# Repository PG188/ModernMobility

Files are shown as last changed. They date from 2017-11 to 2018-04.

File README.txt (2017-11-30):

# ModernMobility
2017-2018 Tron Capstone

The objective of this project is to create a smart, semi-autonomous, medical walker. The lists below include the primary and secondary goals identified for this project. These goals are the anticipated features for the target user within this design project. 

#Primary Goals
1. Modify a standard walker to autonomously drive itself away to a ‘station’ when the user no longer requires the walker. The walker can autonomously track, navigate, and move to the a predefined ‘stations’. 
2. User can remotely prompt the walker to return to them from the product’s current location. 
3. The walker will be capable of actively braking upon detecting any rapid changes in elevation. For example, if a steep slope, stairs, or a sudden drop in the ground is detected. 
4. Maintain the primary functionalities of the common medical walker while augmenting its functionality by adding features in line with the above goals.

#Usefull GIT commands
##fetch all files from master
git fetch origin
git reset --hard origin/master

##git Resources
https://www.git-tower.com/blog/git-cheat-sheet

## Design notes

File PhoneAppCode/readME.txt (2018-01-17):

/**READ ME
* Currently app acts only as a Bluetooth client
* CAN establish a connection with a Bluetooth server
* CAN send data to server once Bluetooth connected
* CANNOT enable devices' Bluetooth
* CANNOT scan for other Bluetooth devices
* CANNOT pair with other Bluetooth devices*/

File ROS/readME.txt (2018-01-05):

Current files:
- Differential_drive is the prebuilt package that converts the velocity command from the navigation stack into individual motor torque commands to be executed by the motor controller
- node_test_1 is a package that contains the incomplete implementations for the nodes that will perform motor control and communication with the arduino connected to the ultrasound sensors. It also launches the differential_drive package, which interacts with the aforementioned nodes to create a complete control loop. 

Trying node_test_1: To try these, you must copy both the differential_drive and node_test_1 folders in your catkin workspace. You must then build them by running catkin_make in your catkin workspace directory. You must then run the launch file in the node_test_1 package using roslaunch. 

You may receive an error about 'Pyside'. To remedy this, execute the following commands which will install the correct files you need:
sudo add-apt-repository ppa:pyside
sudo apt-get update
sudo apt-get install python-pyside

This directory is for files related for ROS applications.

ROS PI SETUP:
Set up
1) Download SD Card Formatter:https://www.sdcard.org/downloads/formatter_4/
2) Download Win32DiskImager: https://sourceforge.net/projects/win32diskimager/
3) Download UBUNTU image: https://ubuntu-mate.org/download/
4) Run SD Card Formatter, select the drive that you have your SD card connected to (i.e. drive E:) and format the SD Card (it will be wiped) 
5) Extract the ubuntu-mate .img file
6) Run Win32DiskImager, select the ubuntu-mate .img file, and have it write to the drive with your SD card that you just formatted
7) Put SD card into pi, power it on, go through ubuntu-mate initial settings
8) Open terminal in ubuntu-mate and follow the ROS install instructions: http://wiki.ros.org/kinetic/Installation/Ubuntu (use full desktop install)

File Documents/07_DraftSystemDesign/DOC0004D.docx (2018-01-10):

# DRAFT SYSTEM DESIGN

# DOCUMENT

MECHATRONICS 4TB6

GROUP 2

NATHAN FUJIMOTO

PRAKHAR GARG

JOSH GILMOUR

AARON JASS

TYLER JASS

FAUZIA KHANUM

JACK LIU

GAGAN SINGH

# Table of Contents

# Table of Figures

# Table of Tables

# Revision History

Rev | Author(s) | Description of Change | Peer Reviewed | Date
- | T.Jass | Original Document | T.Jass A.Jass N.Fujimoto J.Gilmour P.Garg G.Singh F.Khanum J.Liu | 01-Dec-2017
A | T.Jass A.Jass N.Fujimoto J.Gilmour P.Garg G.Singh F.Khanum J.Liu | Added initial rough draft of content. | T.Jass A.Jass N.Fujimoto J.Gilmour P.Garg G.Singh F.Khanum J.Liu | 05-Dec-2017
B | T.Jass A.Jass N.Fujimoto J.Gilmour P.Garg G.Singh F.Khanum J.Liu | Added first draft of diagrams and added more content. | T.Jass A.Jass N.Fujimoto J.Gilmour P.Garg F.Khanum | 14-Dec-2017
C | T.Jass A.Jass N.Fujimoto J.Gilmour P.Garg F.Khanum | Updated diagrams and refined content. | T.Jass A.Jass N.Fujimoto J.Gilmour P.Garg F.Khanum | 20-Dec-2017
D | T.Jass A.Jass N.Fujimoto J.Gilmour P.Garg F.Khanum | Filling in missing content and finalized report format. | | 21-Dec-2017

# Purpose

This document’s purpose is to define and portray the overall system design of all the SmartWalker capstone project. The designs in this document considers all system requirements, defined in the SmartWalker System Requirements document. The document will communicate all the necessary designs for each functional component of the SmartWalker. By the end, the reader should have a clear understanding of what each component is, and how its design meets and satisfies the requirements. The System Design document will be used to begin implementation of the SmartWalker.

# Scope

The scope of this project is to design a walker with autonomous abilities to operate within a specific environment. The operating environment includes and is limited to the inside of a hospital (Patient rooms, staff lounges, hallways, common space). This does not include outside property belonging to a hospital. Outside of the operating environment the SmartWalker will operate as a standard wheeled medical walker.

This project will include (in scope) the following items:

- Autonomous driving (see Section 7.1 for details) between the user and docking station within one indoor room at a time. The docking station is a temporary storage location with charging capabilities.
- Obstacle avoidance in Autonomous mode.
- Assistive walking when using the SmartWalker is in Manual mode (see 7.2 Manual for details).
- Emergency braking (See section 8 for details) if approaching a steep drop in elevation (such as a staircase).
- Location tracking of the SmartWalker within the operating environment.

This project will not include (out of scope) the following items:

- Autonomous usage in multiple indoor rooms simultaneously (autonomous movement is limited to one room).
- Global Positioning system (GPS) tracking

The end result of this project will demonstrate the students’ cumulative learning through their academic career via a demonstration of the SmartWalker’s autonomous ability in a predetermined location. The SmartWalker herein referred to as walker.

# 1 Context Diagram of Boundaries

The System Context Diagram gives a high-level overview of the information passed to the major system components. The entities and interactions between them are described in Table 1 - Entity Descriptions and Interactions. More detailed information can be seen in 2 System Data Flow Diagram.

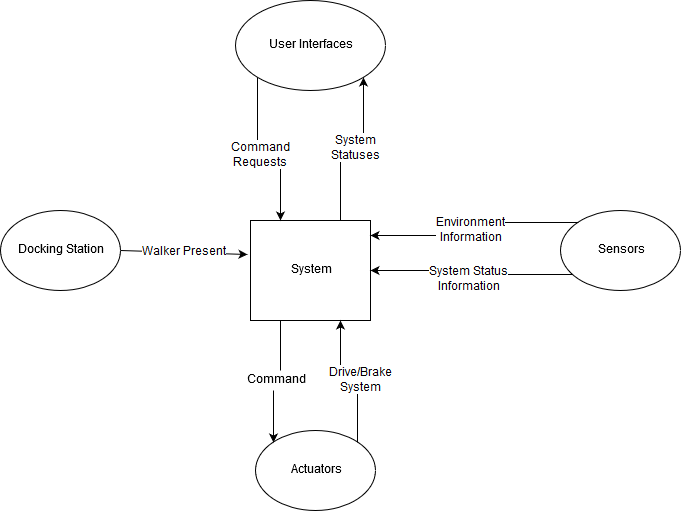
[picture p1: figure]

Figure 1 - Context Diagram of Boundaries

Table 1 - Entity Descriptions and Interactions

Entities | Entity Description | Entity Interactions | Interaction Description
System | The core of all operations. The "system" manages all of the information, computes required information, and outputs information needed by other entities. | See rows below.
User Interfaces | These are the components that the user uses to interact with the system, this would include the phone application and the on-board touch screen. | Command Requests | This will usually be a request to move to a target location or to stop.
| | System Statuses | This is any information about the system that may be useful to the user; Including the battery level, the operational mode of the walker, and the walker's current state.
Docking Station | The docking station is the walker's "Home", it is where it goes to charge. | Walker Present | Indicates to the system whether or not the walker is physically attached to the docking station.
Actuators | Components that execute a physical action. This would include the system's motors. | Command | Commanded operation to the actuator.
| | Drive/Brake System | The output action of the actuator based on the command received.
Sensors | Components that monitor and measure environment or internal information. This information would include the system's camera vision sensor, proximity sensors, and encoders. | Environment Information | Information gathered by the depth and proximity sensors used in obstacle avoidance and navigation.
| | System Status Information | Sensors that retrieve information about the system, such as encoder counts or battery level.

# 2 System Data Flow Diagram

The system Data Flow diagram shows how the different components of the system interact with each other, and with their respective inputs and outputs. The centre of all operations is the Raspberry Pi, which is effectively both the brain and the lesion controlling the flow of all information going in and out of the system.

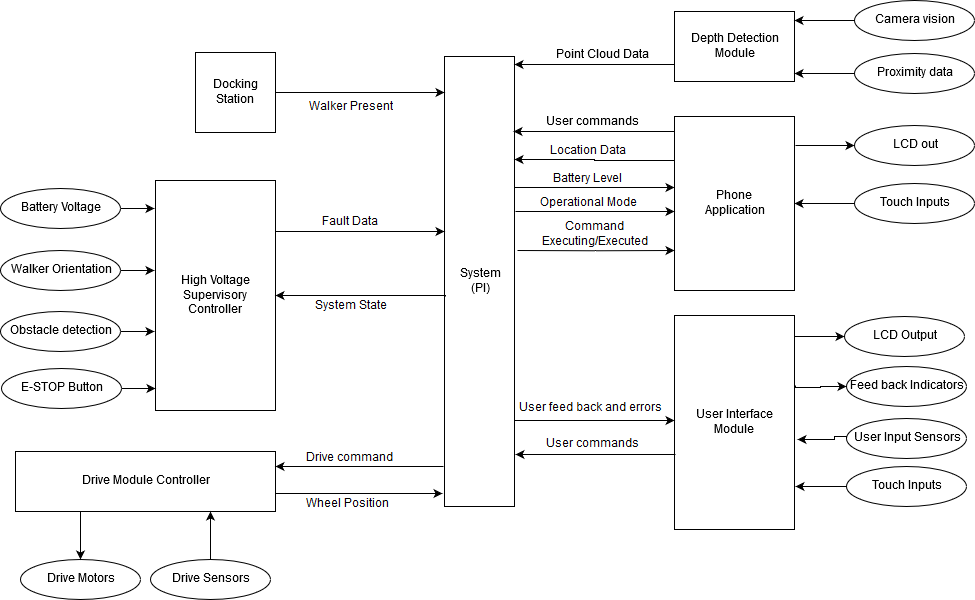
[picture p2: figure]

Figure 2 - System Data Flow Diagram

# 3 Monitored and Controlled Variables

Table 2 - Monitored Variables

Variable | Description | Units | Range
m_battery_lvl | Power level of battery. | Battery Sustain of Charge (%) | [0, 100]
m_battery_rel | Reliability of the battery. | Battery Health (%) | [0, 100]
m_proximity_in_L | Proximity to any objects in the environment (front-left side). | Distance (cm) | [0, 500]
m_proximity_in_R | Proximity to objects in the environment (front-right side). | Distance (cm) | [0, 500]
m_depth_in | Depth of the upcoming ground with respect to the bottom of the walker. | Distance (cm) | [-100, 0]
m_walker_yaw | Orientation of the walker (yaw) with respect to the walker’s z-axis. | Angle (deg) | [-180, 180]
m_walker_pitch | Orientation of the walker (pitch) with respect to the walker’s y-axis. | Angle (deg) | [-45, 45]
m_walker_loc_out | Global location of the walker. | [Longitude (deg), Latitude (deg)] | [-180, 180; -90,90]
m_walker_loc_in | Location of the walker inside the patient room, with respect to a preset coordinate system. | [x,y] on room map | [0, 100; 0, 100]
m_human_loc_in | Location of the human based on their phone, with respect to a preset coordinate system. | [x, y] on room map | [0, 100; 0, 100]
m_human_yaw | Orientation of the human (yaw) with respect to the human’s z-axis. | Angle (deg) | [-45, 45]
m_desired_loc | User selected desired location for the walker in autonomous mode | Enum (states) | GoDocking, GoHuman
m_dock_aligned | Walker is physically aligned with the docking station | Boolean | 0, 1
m_user_in_L | Desired forward assisted movement for the user, for the left motor. | Custom | [-100,100]
m_user_in_R | Desired forward assisted movement for the user, for the left motor. | Custom | [-100,100]
m_emergency_signal | Signal for monitoring an emergency situation. | Boolean | 0, 1

Table 3 - Controlled Variables

Variable | Description | Units | Range
c_motorL_speed | Left motor speed. | Angular velocity ( deg/s) | [0, 50]
c_motorR_speed | Right motor speed. | Angular velocity (deg/s) | [0, 50]
c_brakeL_position | Left brake position. | Brake Position (%) | [0, 100]
c_brakeR_position | Right brake position. | Brake Position (%) | [0, 100]
c_charge_walker | Charge the walker. | Boolean | 0, 1
c_dock_connected | Walker physically connected to the docking station. | Boolean | 0, 1

# 4 Constants

1. Number of kinect sensors
2. Location and orientation of kinect sensors
3. Number of ultrasound sensors
4. Location and orientation of ultrasound sensors
5. Location and orientation of docking station
6. Reference orientation of the user and robot
7. Origin of estimote coordinate frame
8. Location of estimotes in the room
9. Overall walker shape (parameter of differential package in ROS)
10. PID Coefficients for motor controllers
11. Voltage the walker runs on
12. Number of Arduinos
13. Number of Raspberry Pis
14. Number of motor-actuated wheels, motor control boards, and encoders
15. Maximum speed of the walker during autonomous navigation
16. Minimum allowable distance to obstacles while autonomously navigating
17. Distance in front of user that walker should initially navigate too
18. How close the walker should come to the user after initial navigation

# 5 Behaviour Overview

## 5.1 Overall System Behaviour

The behaviour of the walker system can be seen by the following behavioural state diagrams. To describe at the main behavioural components of the walker system, three state diagrams were outlined: the overall system behaviour diagram, the autonomous behaviour diagram, and the manual mode behaviour diagram. The latter two main sub states in which the walker primarily operates in. In any state, the walker is perceiving information from the environment for both functioning and state transitioning.

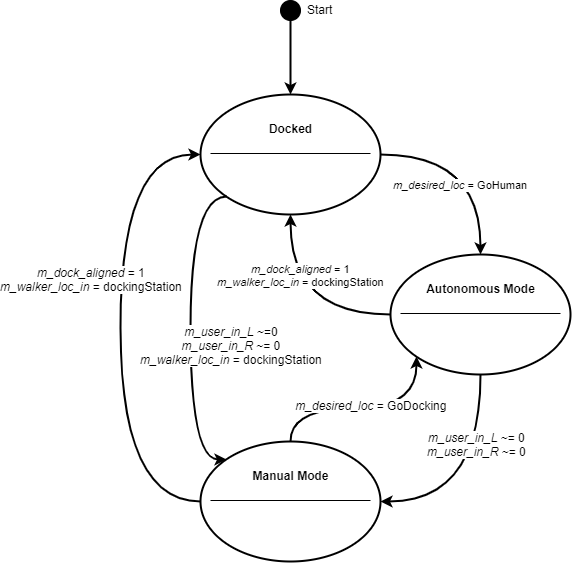
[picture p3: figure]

Figure 3 - Overall System Behaviour Diagram

Table 4 - State Behaviour

State | Description
Docked | In this state the walker is physically connected to the docking station. When connected, the walker is charging its onboard power supply.
Autonomous Mode | In this state the walker is autonomously navigating to and from the user and the docking station (or its current position).
Manual Mode | In this state the walker is being manually operated by the user. This is intended as standard walker usage, with additional safety features.

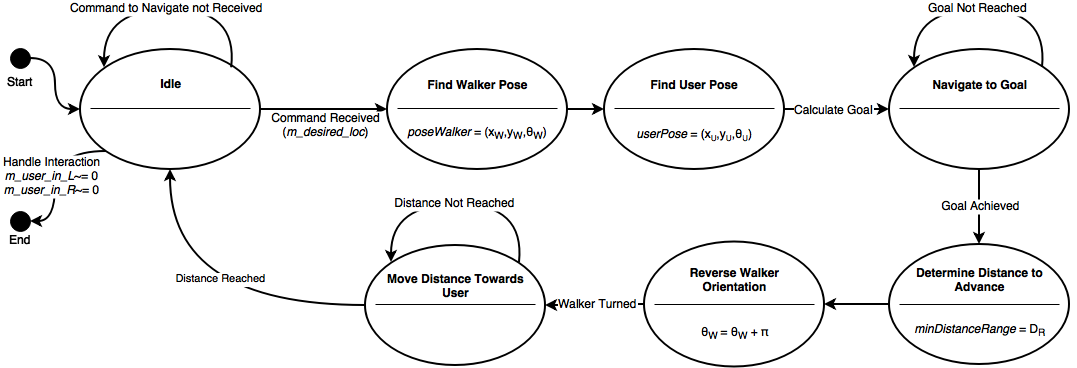
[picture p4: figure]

Figure 4 - Autonomous Mode Behaviour Diagram

Please note, whenever the walker is put into an unintended event, a safety check will be done of the status of the system, and the status will be fixed if possible and sent back to the idle position.

Table 5 - Autonomous Mode States

State | Description
Idle | In this state the walker is in a waiting phase where it is waiting on instructions on where to navigate by the user, via the user interface.
Find Walker Pose | In this state the walker determines its relative position on the constructed map grid, as well as its relative yaw angle on the map.
Find User Pose | In this state the walker system determines the relative position of the user on the constructed map grid, as well as the user’s relative yaw angle on the map.
Navigate to Goal | In this state, considering the walker pose and user pose, the walker calculates the navigation goal and thus begins to navigate to the location.
Determine Distance to Advance | In this state the walker determines how far it can safely approach the destination.
Reverse Walker Orientation | In this state the walker orientates its yaw relative yaw angle so that its handles are facing the user (180-degree turn).
Move Distance Towards User | In this state the walker creeps until it has reached the safe approaching distance. The system then goes back to the idle state.

As described in the overall system behaviour diagram, if either the walker has reached the docking station or the user physically interacts with walker will the behaviour exit the autonomous mode.

## 5.2 Navigation Goal Calculation

The walker and user pose will both be determined by the beacons in the room. The goal is the location where the robot is supposed to travel based on where the user is. The goal is calculated to be some distance, K, in front of the user. It is calculated as:

Figure 5 - Navigation Goal Calculation

The pi added to the user orientation ensures that the walker is facing the user at the end of navigation. This facilitates the measurement of distance between the walker and user in the next state. The walker is then to turn around and approach the user to a reasonable distance (to be determined).

Figure 6 - Manual Mode Behaviour Diagram

Table 6 - Manual Mode States

State | Description
Idle | In this state the walker is in a waiting phase where it awaits physical interaction from the user, in the form of the handle sliders being moved.
Check if Walker is Safe | In this state the walker immediately checks the environment if there are any detectable dangerous obstacles or landmarks in the vicinity of the walker.
Walker in Use | Once the system deems it is safe, in this state the walker operates like a traditional walker, where it helps the user move him or herself.
Emergency Detected | In this state an emergency was detected and the walker brakes so it cannot be further moved. A safety check is completed so the emergency situation is no longer present.

Please note, the Emergency Detected includes the detection of any hazardous situations the user is in the vicinity of (oncoming drops, large slopes, etc..). The safety check will enact functionality to aid the user if wished to proceed through the hazard, if possible (please refer to Section 7 - Normal Operation) Manual mode behaviour is left when the user asks for the walker to navigate back to the docking station, or to a new position where the user would be.

# 6 Component Details

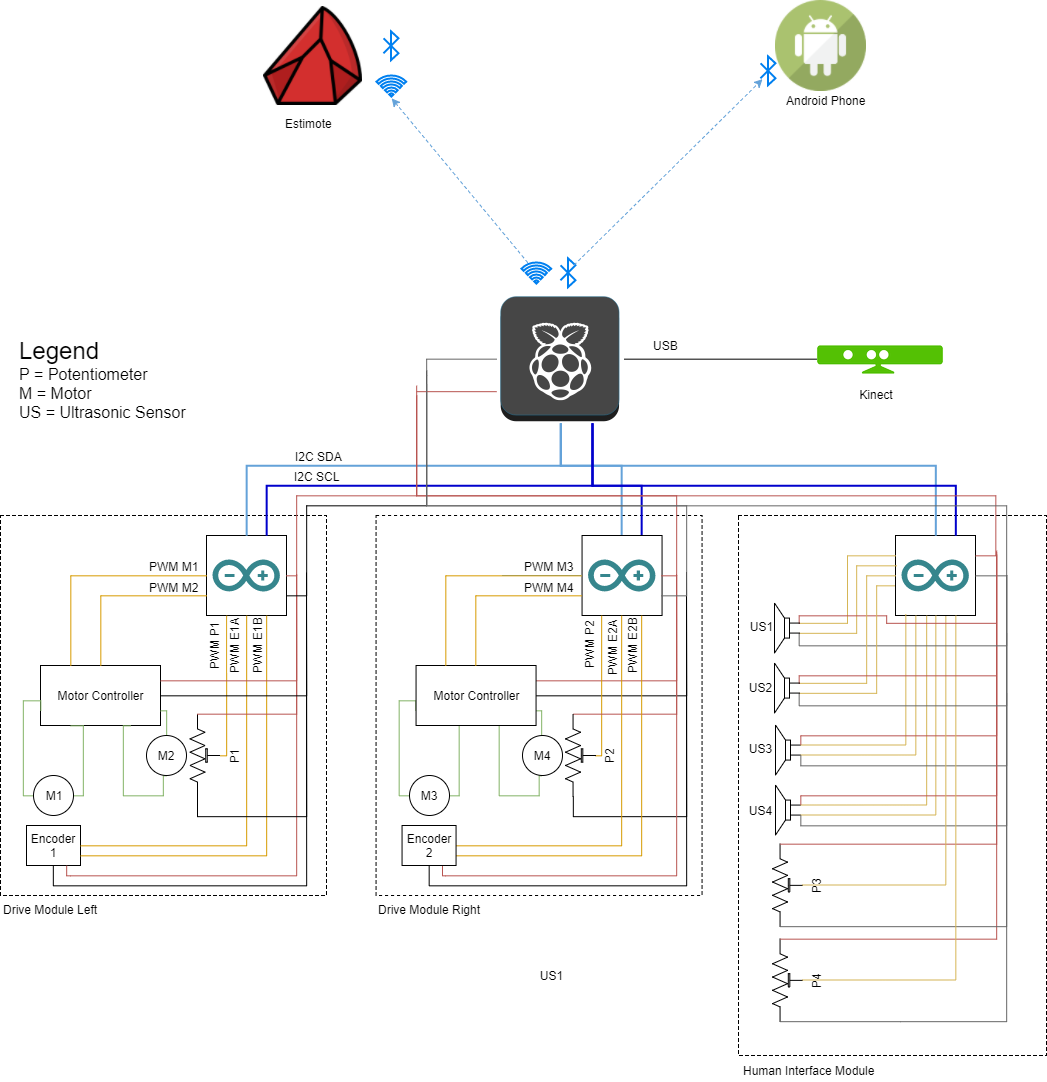
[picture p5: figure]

Table 7 - Component Descriptions

Component | Inputs | Outputs | Description
Raspberry Pi | Modules: - Microsoft Kinect - Estimotes - Android Mobile Phone | Modules: - Drive Module Left - Drive Module Right - Human Interface Module | The main supervisory module in the walker System. It directs data to and from the other modules to assure functionality.
Estimotes | Monitored Variables: - m_walker_loc_in | Modules: - Raspberry Pi | Wireless beacons to be used for indoor location and navigation of the walker System.
Android Phone | Monitored Variables: - m_human_loc_in - m_human_yaw - m_desired_loc | Modules: - Raspberry Pi | The assumed personal electronic device that is owned by the user. This device will host the walker Application that will transmit commands and user location information, and receive system system status information.
Kinect (Sensory Module) | Monitored Variables: - m_proximity_in_L - m_proximity_in_R - m_depth_in - m_walker_yaw - m_walker_pitch | Modules: - Raspberry Pi | Sensor returning point cloud data about the environment. This sensor is vital to the system’s object detection.
Drive Modules | Modules: - Raspberry Pi - Human Interface Module | Control Variables: - c_motorL_speed - c_motorR_speed - c_brakeL_position - c_brakeR_position | Modules that will do computations on the internal system data and external environment data from the sensors and use it to control the actuators (motors) appropriately.
Human Interface Module | Monitored Variables: - m_user_in_L - m_user_in_R - m_emergency_signal Modules: - Raspberry Pi | Modules: - Drive Modules | This module is the physical interface between the drive module and the user. It allows the user to manually drive the walker system’s motors.

Table 8 - Derived Timing Constraints

Module | Derive Timing Constraints
Kinect | Cannot read data from the Kinect faster than the Raspberry Pi can process it whilst also maintaining other system functionality
Android Phone | Will communicate messages from the user at the standard Bluetooth 4.0 speeds to the Raspberry Pi (on the walker), and back to the user.
Estimotes | The beacon responsiveness will adhere to the Raspberry Pi’s scanning of the beacons while in Autonomous Mode.
Raspberry Pi | Must communicate with the arduinos at a rate they can handle and are configured to accept.
Drive Modules | Arduinos must communicate with the Pi and motor controllers at a rate they can handle and are configured to accept. The arduinos must run fast enough that it does not miss any encoder counts and are able to keep up with the rate of them.
Human Interface Module | The status of the human and environment interactions must be checked often enough that no user interactions are missed. Braking inputs and ultrasonic data will adhere to serial ‘I-squared-C’ speeds for sending data to the Raspberry Pi and to the Drive Modules.

Table 9 - Initialization

Module | Initialization
Kinect | Run the libfreenect driver to allow reading data from the Kinect.
Android Phone | The app must be running on the phone and a bluetooth connection established with the walker before several walker features can be used, such as autonomous navigation.
Estimotes | Physically the beacons required to be on the walls of the room, at the centre of each wall. Additionally, one would have to be inside the walker and connected to the Raspberry Pi at initialization.
Raspberry Pi | The Raspberry Pi will be turned on and have the necessary software pre-installed.
Drive Modules | The Arduinos, motor controllers, motors, and encoders will all have to be turned on via power-up. The arduinos will have the necessary software pre-installed.
Human Interface Module | The arduino and the sensors to interact with the human and environment (brakes and ultrasonic) will be initialized at power-up.

# 7 Normal Operation

The following section will describe the different modes and states each mode has in more detail by stepping through possible positive normal scenarios.

Please note since this is the Draft System Design that we have not determined all details yet and have noted said details to be defined later.

## 7.1 Autonomous

As mentioned in our System Requirements document, autonomous mode is the ability to move out to a designated home location as well as return to the user when requested. Autonomous mode consists 3 states: moving to user, moving to docking station, and docked. The following sections will describe positive normal scenarios (behaviour the system should cover and everything proceeds as expected).

### 7.1.1 Moving to user

1. User is not detected by handlebar sensors (m_user_in_L and m_user_in_R)
2. User requests the walker to come to user via phone app
3. Phone app sends bluetooth signal to walker
4. If walker is not within bluetooth distance?
  a. Display message to user “Walker out of reach.”
5. If walker is within bluetooth distance
  a. Walker retrieves walker pose from estimotes
  b. Walker retrieves user pose from estimotes
  c. Walker calculates the goal pose and begins navigating to it, as described before
  d. Once the walker reaches the goal, the distance to the user is measured
  e. The walker turns 180 degrees
  f. The walker backs up to within a reasonable distance from the user
  g. Walker returns to idle state

### 7.1.2 Moving to docking station

1. User is not detected by handlebar sensors (m_user_in_L and m_user_in_R)
2. User sends signal to dock via phone app
3. If walker is not within bluetooth distance
  a. Display message to user “Walker out of reach.”
4. If walker is within bluetooth distance
  h. Walker retrieves walker pose from estimotes
  i. Walker retrieves docking station pose from estimotes
  j. Walker moves to docking station
  k. Walker docks into charging port (m_dock_aligned)
    i. Go to Docked state

### 7.1.3 Docked

1. Walker is at the docking station and connected (c_dock_connected)
  a. If battery is less than 100% (m_battery_lvl)
      1. charge (c_charge_walker)
    i. If battery is at 100% (m_battery_lvl)
      1. Disengage charging and go to Idle state

## 7.2 Manual

As mentioned in our System Requirements document, Manual mode is the ability to operate like a standard medical walker, with added smart features such as assisted braking and assisted driving. Manual mode has 4 states: regular walking, slope change, objects detected, and idle. The following sections will describe positive normal scenarios (behaviour the system should cover and everything proceeds as expected).

### 7.2.1 Regular Walking

This state is when the user is utilizing the walker as intended; aiding in regular walking.

1. User detected at handlebar sensors (m_user_in_L and m_user_in_R)
  a. Detect if the walker is moving and surrounding environment
    i. Slope change → Slope Change mode
    ii. Objects in way → Objects detected
    iii. User is utilizing walker for normal walking
  b. User applies brakes manually (c_brakeL_position and c_brakeR_position)
    i. reduce speed accordingly
2. If user is not detected (for more than a certain amount of time, to be determined)
  a. Enter idle state

### 7.2.2 Slope Change

This state is for when the user is detected at the handlebar sensors, the user is walking around with the aid of the walker and the smartwalker has detected a change in slope of the ground.

1. Query the slope of the ground using the onboard sensors
2. Calculate the pitch of the walker (m_walker_pitch)
3. If the pitch of the walker is positive or negative 5 deg to a certain deg
  a. This state has yet to be finalized, more details to come in the future

### 7.2.3 Idle

1. User is not detected at handlebar sensors (m_user_in_L and m_user_in_R)
  a. If walker is not detected at docking station (m_dock_aligned)
- Walker waits for command from user
  b. If walker is detected at docking station (m_dock_aligned)
    - If battery is less than 100% (m_battery_lvl)
      - charge walker (c_charge_walker)
    - If battery is 100% (m_battery_lvl)
      - Sit idle (details of idle mode to be determined)

# 8 Undesired Event Handling

Section 7 covered normal operation of the walker, this section will talk about abnormal scenarios and how the walker will handle them. Each section will describe the undesired event and the steps the system will take to ensure that the event is resolved in a safe manner.

## 8.1 Emergency Stop

Emergency stop refers to when the user pushes/applies the emergency stop or the system determines that there is an emergency and sends a signal at any point while the walker is in normal operation. This option is for when the user

1. Emergency Stop activated
  a. Brakes applied to motors in a safe manner (c_brakeL_position and c_brakeR_position)
  b. State of emergency (walkerSafe = False)
  c. Display prompt for user to cancel emergency state
  d. Wait for user input
    i. Safe to continue OR enter manual mode (cancel initial request)

## 8.2 User Detected During Autonomous Mode

The following scenario is for the walker is in autonomous mode and a user is detected by the handlebar sensors.

1. Walker is in autonomous mode
2. User is detected by handlebar sensors (m_user_in_L and m_user_in_R)
a. Brakes applied to motors in a safe manner (c_brakeL_position and c_brakeR_position)
b. Walker enters manual mode

## 8.3 Object Collision with Smartwalker

The following scenario is for when the smartwalker is in autonomous mode and has collided with an object of a minimum size yet to be determined.

1. Walker location does not match expected location
a. Brakes applied to motors in a safe manner (c_brakeL_position and c_brakeR_position)
b. State of emergency (walkerSafe = False)
c. Wait for user input
  i. Safe to continue OR enter manual mode (cancel initial request)

## 8.4 Walker has Fallen Over or Very high Incline/Decline

This state is when the walker has fallen over or is at a dangerously high incline or decline. This is a very undesired and not recommended.

1. Walker gyroscopes detect angle greater than 15°
a. Brakes applied to motors in a safe manner (c_brakeL_position and c_brakeR_position)
b. State of emergency (walkerSafe = False)
c. Wait for user input
  i. Safe to continue OR enter manual mode (cancel initial request)

## 8.5 Goal location is unreachable

When the walker is in autonomous mode, it has a goal of either the user or the docking station. In moments when the path is not clear to the destination, the following will occur:

1. Walker attempts to reach destination
2. Several attempts at reaching goal occur (attempt number and duration to be determined)
3. Walker stops attempting to reach goal
4. Go into idle mode
5. Message is sent to the user’s phone “unable to reach destination.”

## 8.6 Walker cannot “see”

The following state refers to when the walker sensors are not functioning properly either due to sensor malfunction or a blockage (items covering the sensors) and therefore reporting false data. The walker is in an environment it is not capable of reliably navigation through and thus navigation will cease autonomous mode and the walker will return to manual mode. The user is then able to move the walker to a safe location for troubleshooting.

## 8.7 Walker is unable to move while autonomously navigating

When the walker is in Autonomous mode and Autonomous navigation with cease and the walker will return to idle mode. The user will be notified via the phone application of the problem.

## 8.8 Extremely low battery

Since the walker is very dependent on power, when the battery level is very low (low level to be determined) the walker will the take the following actions.

1. User will be notified of the low battery state via the phone application
2. The walker will shut down to avoid unexpected behaviour at low power and to avoid damaging the battery

# References

Rodriguez, J. (2016, November 22). How An ADA Compliant Ramp Must be Built. Retrieved December 21, 2017, from https://www.thebalance.com/ada-ramp-construction-844440

MODERN MOBILITY DRAFT SYSTEM DESIGN DOCUMENT Doc: DOC0004 Rev: D

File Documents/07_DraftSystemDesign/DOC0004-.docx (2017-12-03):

# DRAFT SYSTEM DESIGN

# DOCUMENT

MECHATRONICS 4TB6

GROUP 2

NATHAN FUJIMOTO

PRAKHAR GARG

JOSH GILMOUR

AARON JASS

TYLER JASS

FAUZIA KHANUM

JACK LIU

GAGAN SINGH

Table of Contents

# Table of Tables

# Revision History

Rev | Author(s) | Description of Change | Peer Reviewed | Date
- | T.Jass A.Jass N.Fujimoto J.Gilmour P.Garg G.Singh F.Khanum | Original Document

# Purpose

# Scope

# 1 Context Diagram of Boundaries

2 System Component Diagrams

3 Monitored and Controlled Variables

4 Constants

5 Behaviour Overview

6 Component Details

7 Normal Operation

8 Undesired Event Handling

References

## 2.1 Tools and Versions

Table 2 - Tools and Versions

Tool | Version | Purpose/Function

Software Tools:
Google Drive | N/A | Storage accessible by entire group for deliverable documents.
Google Docs | N/A | Real-time collaboration.
Draw.io | N/A | Online web tool for model mapping and flow chart development.
Git | 2.15 | Software Version control, deliverable document, and internal document storage.
Ubuntu MATE | 3.0 | OS being used on our systems controller (Raspberry Pi 3B).
ROS (Robotics Operating System) | Kinetic | Robotics operating system library being used to develop project’s autonomous navigation capabilities.
Android Studio | 3.0 | Environment for Android App Development.
Autodesk Inventor | 2017 | Model all physical Robotics systems.

Mechanical Tools:
3D Printer | N/A | Prototype any mechanical parts for motor and braking systems.
Hand Drill | N/A | Used for drilling holes
Saw | N/A | Used for cutting material
CNC Mill | N/A | Produce finished mechanical parts for motor and braking systems.

Electrical Tools:
Soldering Iron | N/A | Soldering wires/ circuit boards
Multimeter | N/A | Measure voltage and current
Power Supply | N/A | Powering prototype circuits/Motors
Oscilloscope | N/A | Measuring electrical signals

## 2.2 Special Instructions

All document resources will be backed up to the corresponding version control systems.

## 2.3 Standards Followed

- All code should be commented to allow for quick and painless troubleshooting, our motto is “Comment as if the next person who reads your code is a serial killer”
- When coding, no function should have more lines than what can be seen on your computer screen at one time
- No software or hardware tested by the person who implemented it can deemed “Working” (basically do not test your own work, get someone else to test it)
- Metric Units will be used for all modeled components

## 2.4 Delegation of Steps

Legend

1 - Primary Responsibility

2 - Secondary Responsibility

3 - Tertiary Responsibility

Highlight - Persons Responsible for section of project

Table 3 - Delegation of Steps

| Josh | Aaron | Jack | Nathan | Fauzia | Prakhar | Tyler | Gagan
Phone application development | | 1/2 | 1 | | 3 | 2 | 3
Autonomous navigation software | 1 | | 2 | 2
Low-level software | 2 | 3 | | 1 | 1 | | 1
System integration | 3 | | 3 | | 2 | 1* | | 3
Wheels and brakes modifications | | 1/2 | | 3 | | 3 | 2 | 1
Handle Bar (brake interference) | | | | | | 1 | | 2

# 3 How Version Control is Being Used

Version control will be used to manage all source code, and as well as store documents. The source code will be organized into different directories based on the application. Documents including will be both deliverables and internal documents used for team knowledge sharing.

Our Git is organized into folders that relate to different aspects of the project. These folders are described in the table below.

Table 4 - Git Organization

Folder | Purpose
CADs | Store the CAD files created of the walker and other components
Low level | Store documentation and files related to the software built for the Arduino and Raspberry Pi
Phone application code | Store documentation and files related to the phone application that is used to control and setup the walker.
ROS | Store documentation and files related to the ROS software on the walker

# 4 Dealing with Changes to Artifacts

## 4.1 Bug Tracking/Change Request Tool

If we find that we are running into a lot of bugs and are spending quite a bit of time resolving them we will look into using Bugzilla. It is free for any number of users, compatible with Linux, MacOS, and Windows, and contain the following:

- Time tracking
- Reporting
- Duplicate bug detection
- Customization: custom fields to suit application

## 4.2 Documentation of Change Requests/Bugs

All of documentation is first drafted in Google Docs. Google Docs allows real time collaboration, commenting, and revision control. We can use this to document and track changes during the creation and drafting process. Once complete, we can export to word and finalize the document.

## 4.3 Classification of Changes

Changes will have different statuses such as:

- In queue (Waiting to be dealt with)
- Working (Currently being investigated)
- Resolved (Issue/Bug successfully dealt with)
- Unresolved (Unable to solve this issue/bug)

They should also have different levels of urgency based on how core the issue/bug is to the particular systems functionality.

## 4.4 Disposition of Changes

Change statuses will be verified and changed to different status by the appropriate party. For example, anyone can raise an issue and add them to “In Queue”. Depending on the given issue, a particular team may be responsible to fix that issue. Only that team can change that issue’s status to “Working”. Since it would bad practice to have the same person who fixed the issue, also verify the issue, someone else would be responsible for moving the issue to “Resolved”. If the person fixing the issue cannot fix it, they can move it to “Unresolved” so someone else can try it.

MODERN MOBILITY DRAFT SYSTEM DESIGN DOCUMENT Doc: DOC0004 Rev: -

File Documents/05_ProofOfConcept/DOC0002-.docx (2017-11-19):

# PROOF OF CONCEPT

# TEST REPORT DOCUMENT

MECHATRONICS 4TB6

GROUP 2

NATHAN FUJIMOTO

PRAKHAR GARG

JOSH GILMOUR

AARON JASS

TYLER JASS

FAUZIA KHANUM

JACK LIU

GAGAN SINGH

# Revision History

Rev | Author(s) | Description of Change | Peer Reviewed | Date
- | T.Jass | Original Document | N. Fujimoto A. Jass | 19/11/2017

# Document References

N/A

# Table of Tables

N/A

# Table of Figures

N/A

# 1 Required Knowledge

## 1.1 Image of Kinect

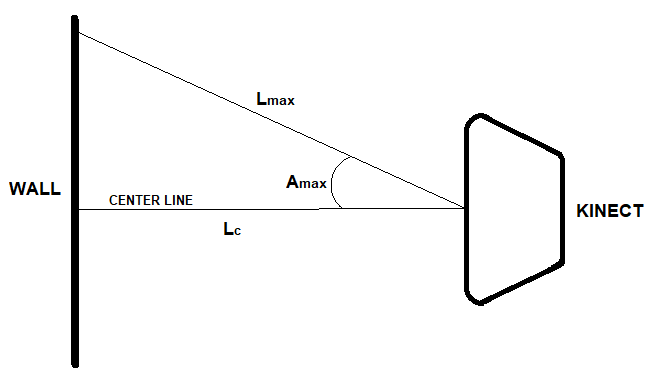
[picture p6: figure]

## 1.2 Terminology

Term | Definition
Kinect | Microsoft’s Kinect Camera
Wall | Flat wall surface used in testing
Center Line | Line of sight going straight (angle of 0 degrees) to the wall
Amax | Maximum angle from the centre line the Kinect can detect
Lmax | Length from the Kinect’s Camera to the wall at an angle of Amax
Lc | Length from the Kinect’s Camera to the wall along the center line

# 2 Procedure

1. Faced Kinect toward the wall, ensuring that the line of sight going straight was perpendicular to the wall.
2. Physically measured using a measuring tape and positioned the Kinect so that Lc = 50cm.
3. Recorded the Lc value measured by the Kinect.
4. Physically measured using a measuring tape the Lmax value.
5. Recorded the Lmax value measured by the Kinect.
6. Repeated steps 2 to 5 for Lc = 75cm, 100cm, and 125cm.
7. Repeated steps 2 to 3 for Lc = 192cm and 213cm.

# 3 Results

<Insert Graphs and excel table data>

MODERN MOBILITY PROOF OF CONCEPT TEST REPORT DOCUMENT Doc: DOC0002 Rev: -

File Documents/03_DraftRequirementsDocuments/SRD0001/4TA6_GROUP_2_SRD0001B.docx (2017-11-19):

# SMART WALKER

# SYSTEM REQUIREMENTS DOCUMENT

MECHATRONICS 4TB6

GROUP 2

NATHAN FUJIMOTO

PRAKHAR GARG

JOSH GILMOUR

AARON JASS

TYLER JASS

FAUZIA KHANUM

JACK LIU

GAGAN SINGH

Table of Contents

# Revision History

Rev | Author(s) | Description of Change | Peer Reviewed | Date
- | T.Jass | Original Document | A.Jass | 10-Oct-2017
A | N.Fujimoto P.Garg J.Gilmour A.Jass T.Jass F.Khanum J.Liu G.Singh | Original document was blank with just a layout. This revision adds content to the document. | N.Fujimoto P.Garg J.Gilmour A.Jass T.Jass F.Khanum J.Liu G.Singh | 01-Nov-2017
B | N.Fujimoto P.Garg J.Gilmour A.Jass T.Jass F.Khanum J.Liu G.Singh | Edited Functional Requirements, functional decomposition diagrams and variables, non-functional requirements. Added Systems Definitions and Requirements Subject to Change Sections. | N.Fujimoto P.Garg J.Gilmour A.Jass T.Jass F.Khanum J.Liu G.Singh | 06-Nov-2017

# Table of Tables

# Table of Figures

# 1.1 Introduction

## 1.1 Purpose

The standard medical walker or walking aid helps to improve the stability and balance of its user while they are walking. The objective of this project is to modify a standard medical walker to include various mechanical/electrical components and autonomous features in order to improve the user experience. The modified walker, called the SmartWalker, will involve designing and developing an autonomous and safe system while keeping all original functions of the standard medical walker.

This document defines the project scope, outlines the system overview and highlights the main functional and nonfunctional requirements of the SmartWalker.

## 1.2 Project Scope

The scope of this project is to design a walker with autonomous abilities to operate within a specific environment (refer to section 2.4 Operating Environment). The SmartWalker will feature:

- Autonomous driving between a docking location and the user within an indoor room, and vice-versa. The dock is a temporary storage location with charging capabilities.
- Autonomous obstacle avoidance when driving to and from the user.
- Assistive walking when using the SmartWalker normally, this includes assistive powering when going up ramps, and active braking when going down ramps.
- Emergency braking in any situation if approaching a steep drop in elevation (staircase).
- Global Position System (GPS) tracking within the environment.

This project will not include (out of scope) the following items:

- Autonomous usage in multiple indoor environments simultaneously (autonomous movement between multiple rooms).
  - Autonomous features in an entire hospital.
- Exact GPS tracking while walker is indoors.

The end result of this project will demonstrate the students’ cumulative learning through their academic career via a demonstration of the SmartWalker’s autonomous ability in a predetermined location.

# 2 Overall Description

## 2.1 System Overview

The SmartWalker is an original idea by the Modern Mobility group, within the capstone course of the Computing and Software Department, 4TB6, at McMaster University. The focus of the SmartWalker project is to increase the utility of a standard medical walker by implementing various autonomous and electric features. Full system details and functionalities are explained below.

## 2.2 System Term Definitions

Table 1 - System Term Definitions

Term | Definition
X-axis | Forward direction relative to the SmartWalker.
Y-axis | Left direction relative to the SmartWalker.
Z-axis | Upward direction (normal to the SmartWalker’s XY-plane).
Yaw | Angle from the X-axis going counter-clockwise about the Z-axis in the XY-plane.
Pitch | Angle from the Y-axis going counter-clockwise about the X-axis in the YZ-plane.
Roll | Angle from the Z-axis going counter-clockwise about the Y-axis in the XZ-plane.
Docking Station | The device that charges the SmartWalker. This is considered the SmartWalker’s Home.
UI | User Interface.
Phone App (Phone Application) | Refers to an application on a person’s smartphone device. Often simply called an “App”.

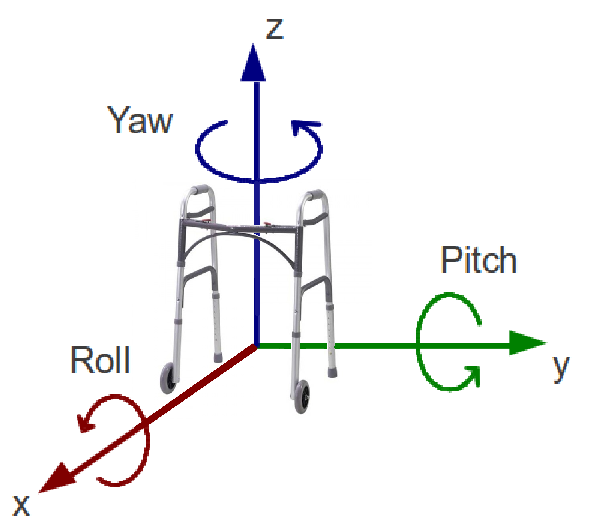
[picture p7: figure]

Figure 1 - SmartWalker Axes and Orientation

## 2.3 System Behaviour

The SmartWalker has two main functionalities (or modes): autonomous mobility and manual driving.

- Autonomous Mode: The ability to move out of the way of the user whenever requested to a designated home location as well as return to the user when requested.
- Manual Mode: The ability to operate like a standard medical walker, with added smart features like assisted braking and assisted driving.

These core functions are supported by two sub-functions: a phone application and a docking station. The phone app is used as an avenue to capture user-specific monitored variables, while the docking station is used to support the autonomous mobility function by acting as a home location.

## 2.4 Operating Environment

The operating environment of the SmartWalker is a typical hospital. This environment is divided into two areas: the patient’s room, and the hospital hallways/common rooms and outside grounds. Manual mode will be available in all environments (patient room, hospital corridors, hospital grounds etc.) while Autonomous mode will only be available in the patient room that contains its corresponding docking station.

Figure 2 below indicates a sample patient room in a hospital. The docking station would be located next to a wall plugged into an electrical outlet ready to charge the walker at any moment. The docking station will not be in the way of medical equipment and medical personnel such as doctors, nurses, and caregivers. Figure 3 below indicates a sample hospital and its surrounding outside grounds that the SmartWalker can be implemented in.

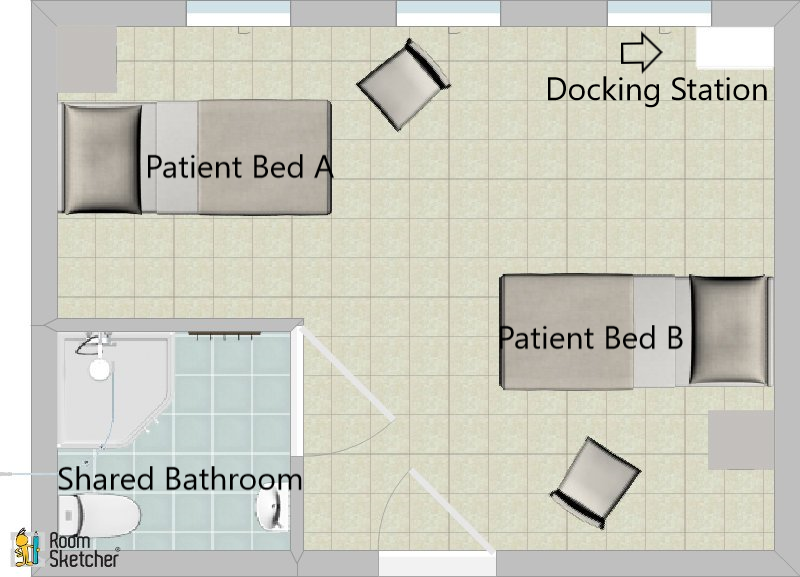
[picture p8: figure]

Figure 2 - Hospital Patient Room

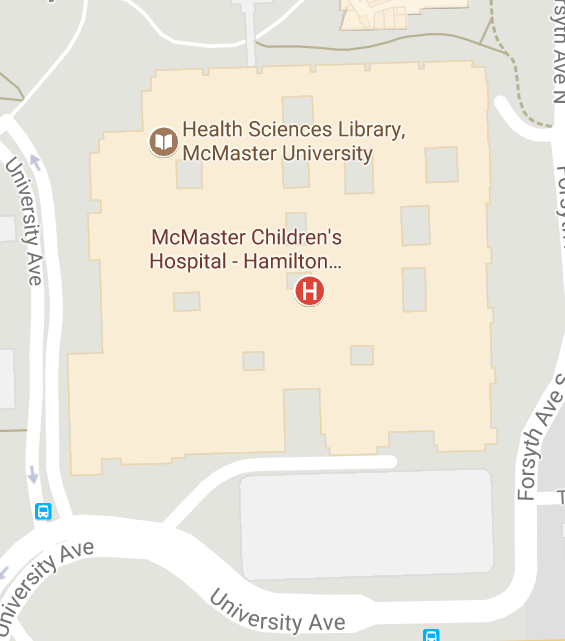
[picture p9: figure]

Figure 3 - Google Maps Image of a Hospital and Surrounding Area

## 2.5 Assumptions

### 2.5.1 Environmental Assumptions

- The SmartWalker will be used in patient rooms that have enough room for wheelchairs to move about, therefore enough room for the SmartWalker to autonomously move about
- It is assumed that the farthest the SmartWalker will be taken will the hospital grounds.

### 2.5.2 Functional Assumptions

- An structurally sound off the shelf walker will be used as the basis for the SmartWalker
- The SmartWalker battery will be charged via the docking station and no other method.

### 2.5.3 User Assumptions

- The user of the SmartWalker will have little experience interacting with technology such as phone applications.
- The user owns a phone that runs on Android OS.

## 2.6 Functional Decomposition and Variables

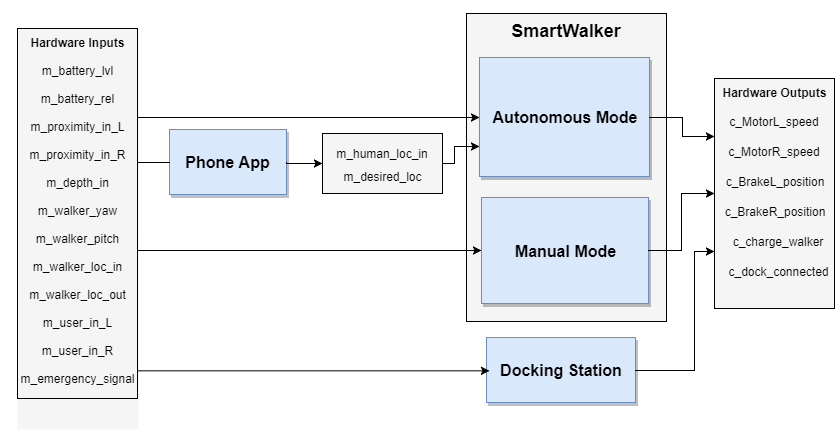
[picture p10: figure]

Figure 4 - Functional Decomposition Diagram

Table 2 - Monitored Variables

Variable | Description | Units | Range
m_battery_lvl | Power level of battery. | Battery Sustain of Charge (%) | [0, 100]
m_battery_rel | Reliability of the battery. | Battery Health (%) | [0, 100]
m_proximity_in_L | Proximity to any objects in the environment (front-left side). | Distance (cm) | [0, 500]
m_proximity_in_R | Proximity to objects in the environment (front-right side). | Distance (cm) | [0, 500]
m_depth_in | Depth of the upcoming ground with respect to the bottom of the walker. | Distance (cm) | [-100, 0]
m_walker_yaw | Orientation of the walker (yaw) with respect to the walker’s z-axis. | Angle (deg) | [-180, 180]
m_walker_pitch | Orientation of the walker (pitch) with respect to the walker’s y-axis. | Angle (deg) | [-45, 45]
m_walker_loc_out | Global location of the walker. | [Longitude (deg), Latitude (deg)] | [-180, 180; -90,90]
m_walker_loc_in | Location of the walker inside the patient room, with respect to a preset coordinate system. | [x,y] on room map | [0, 100; 0, 100]
m_human_loc_in | Location of the human based on their phone, with respect to a preset coordinate system. | [x, y] on room map | [0, 100; 0, 100]
m_desired_loc | User selected desired location for the walker in autonomous mode | Enum (states) | GoDocking, GoHuman
m_user_int_L | Desired forward assisted movement for the user, for the left motor. | Custom | [-100,100]
m_user_in_R | Desired forward assisted movement for the user, for the left motor. | Custom | [-100,100]
m_emergency_signal | Signal for monitoring an emergency situation. | Boolean | 0, 1

Table 3 - Controlled Variables

Variable | Description | Units | Range
c_motorL_speed | Left motor speed. | Angular velocity ( deg/s) | [0, 50]
c_motorR_speed | Right motor speed. | Angular velocity (deg/s) | [0, 50]
c_brakeL_position | Left brake position. | Brake Position (%) | [0, 100]
c_brakeR_position | Right brake position. | Brake Position (%) | [0, 100]
c_charge_walker | Charge the walker. | Boolean | 0, 1
c_dock_connected | Walker physically connected to the docking station. | Boolean | 0, 1

### 2.6.1 Autonomous Mode

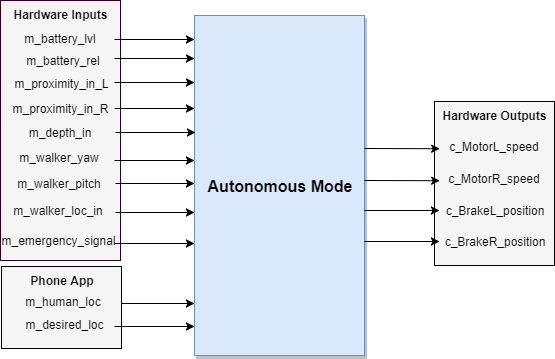
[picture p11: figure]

Figure 5 - Autonomous Mode Diagram

### 2.6.2 Manual Mode

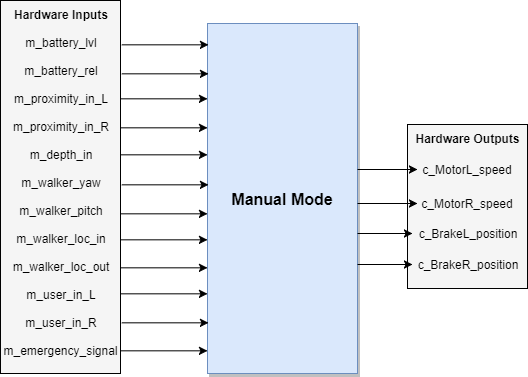
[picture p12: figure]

Figure 6 - Manual Mode Diagram

### 2.6.3 Phone App

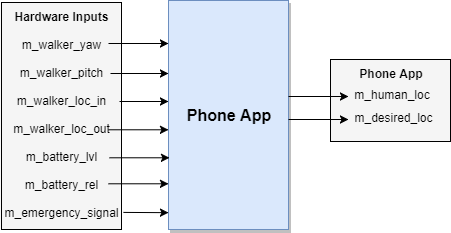
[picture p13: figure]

Figure 7 - Phone App Diagram

### 2.6.4 Docking Station

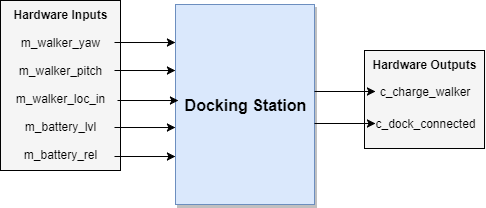
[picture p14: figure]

Figure 8 - Docking Station Diagram

# 3 Specific Requirements

Requirements Subject to change in sections 3.1 and 3.2 are denoted with a “*” at the end of the sentence. These requirements are mentioned again in section 3.3.

## 3.1 Functional Requirements

### 3.1.1 SmartWalker - Autonomous Mode

1. Autonomous Mode shall not be possible if there is no power drawn from the onboard battery.
2. When requested via the phone app, the SmartWalker shall navigate independently to and from the user’s phone location and docking station location.
3. The SmartWalker shall receive its orientation and location information from inputs.
4. The SmartWalker shall receive the phone location and desired destination location.
5. The SmartWalker shall detect how far away objects are in its path.
6. The SmartWalker shall avoid objects in its path.
7. The SmartWalker shall detect the angle of the floor/ground beneath it.
8. The SmartWalker shall detect a rapid change in elevation (e.g. a step) in its path.
9. The SmartWalker shall avoid falling due to changes in its environment.

### 3.1.2 SmartWalker - Manual Mode

1. The SmartWalker shall allow its wheels to roll freely when the e-brake is in the released position.
2. The SmartWalker shall lock its wheels in place when the e-brake is applied.

### 3.1.3 Phone Application

1. The phone application shall receive the SmartWalker’s orientation.
2. The Phone application shall receive the SmartWalker’s location.
3. The Phone application shall receive the SmartWalker’s desired location.
4. The Phone application shall receive the battery’s reliability.
5. The Phone application shall receive the battery’s level.
6. The phone application shall communicate the user’s location to the SmartWalker.
7. The phone application shall communicate the desired location to the SmartWalker.
8. The Phone application shall display the battery’s reliability.
9. The Phone application shall display the battery’s level.
10. The Phone application shall receive a notification if a request failed. *

### 3.1.4 Docking Station

1. The docking station shall charge the on-board SmartWalker battery when it is docked.*
2. The docking station shall lock in the SmartWalker when it is docked.*

### 3.1.5 Driving and Braking Requirements

1. The SmartWalker’s left wheel shall be inactive and roll freely when no request has been made.
2. The SmartWalker’s left wheel shall be active and drive forward when a request has been made.
3. The SmartWalker’s left wheel shall be active and drive backward when a request has been made.
4. The SmartWalker’s left wheel shall only continue moving if a request is continually made.
5. The SmartWalker’s right wheel shall be inactive and roll freely when no request has been made.
6. The SmartWalker’s right wheel shall be active and drive forward when a request has been made.
7. The SmartWalker’s right wheel shall be active and drive backward when a request has been made.
8. The SmartWalker’s right wheel shall only continue moving if a request is continually made.
9. The SmartWalker’s wheel’s linear speeds shall be proportional to the input request.
10. The SmartWalker shall have its brakes released by default.
11. The SmartWalker shall decelerate and an eventual stop when the brakes are requested.
12. The SmartWalker shall come to a complete stop in a safe amount of time when the brakes are requested.
13. The SmartWalker shall not take the walker more than five seconds to begin moving to its destination when requested.

### 3.1.6 Other Requirements

1. The SmartWalker shall be defaulted to Manual Mode on start-up.
2. The SmartWalker shall switch to Auto Mode when given an Auto Mode request.
3. The SmartWalker shall switch back to Manual Mode when the Auto Mode request is completed or failed.
4. The SmartWalker shall turn on when requested.
5. The SmartWalker shall turn off when requested.
6. The SmartWalker shall function as standard non-electric walker there is no power drawn from the onboard battery, or power is disabled.
7. The SmartWalker’s digital UI shall not take more than one second to respond to user input.

## 3.2 Non-Functional Requirements

### 3.2.1 Look and Feel Requirements

1. The walker shall look as close to a standard walker as possible to not draw potentially unwanted attention to the user.
2. All functional components (electronics, motors) shall be enclosed and hidden from view to improve the aesthetics of the walker.

### 3.2.2 Usability requirements

1. Braking the walker shall be possible for those with physical ailments that limit the functionality and dexterity of their hands.
2. The walker shall be easy to autonomously summon by users with physical ailments that limit the functionality and dexterity of their hands.
3. The walker shall be easy to learn to use for elderly unfamiliar with modern technology.
4. The text size in any digital interface can be varied by the user to aid those with poor eyesight because a significant portion of the target market of the walker has poor eyesight.
5. The walker shall not weigh more than 150 pounds to limit the load on the battery from moving the walker. *

### 3.3.3 Performance Requirements

#### Safety Critical Requirements

1. The walker shall not accelerate excessively while in use by the user to ensure safety.
2. Moving components such as disk brakes, servo motors, and induction motors shall be enclosed to prevent injury.
3. The moving component enclosures shall be tough enough that they do not sustain significant damage from minor impacts. This is necessary to ensure user safety throughout the life of the walker.

#### Precision Requirements

4. The walker shall be able to autonomously navigate into the docking station from any location in the room where there is a suitable path to the docking station.
5. The walker shall eventually come within half a meter of the user after being commanded to navigate to the user when there is a suitable path. This will ensure that the walker is close enough to the user that they can reach it.

#### Reliability and availability requirements

6. The walker shall take at most an hour to charge to limit the time where the user cannot use the walkers advanced features.*
7. On a full charge, the walker shall have enough battery for at least twenty minutes of standard usage.*

#### Capacity requirements

8. The product shall be able to support the weight of a single user that weighs at most 300 pounds. This will ensure that the majority of the population can use the walker.*

### 3.3.4 Operational Requirements

#### Expected physical environment

1. The walker is to be used by the elderly or mobility challenged individuals while standing up in an indoor, single-floor environment.
2. The walker is only to autonomously navigate inside environments where doors and other obstructions do not separate the walker from the destination.

#### Expected technological environment

3. The walker must be able to interface with any modern android phone to ensure a large portion of users with phones can utilize the walkers advanced features.*

### 3.3.5 Maintainability and Portability Requirements

1. The application for communicating with the walker is expected to run on Android phones.

### 3.3.6 Security Requirements

1. Only registered caregivers, family, and significant others in a caregiving role shall be given the ability to use the GPS tracking feature of the walker to protect the user's privacy.*

### 3.3.7 Legal Requirements

1. GPS tracking functionality must be easily removed to facilitate sale in areas where such functionality is illegal or may become illegal
2. As a medical device, the walker must meet Canada’s Medical Devices Regulations as outlined in SOR/98-282

### 3.3.8 Open Issues

1. Investigation into the suitability of Google’s Eddystone technology for walker localization is not yet complete.
2. Investigation and testing of the suitability of using a single a Raspberry Pi for all system processing is not yet complete.

### 3.3.9 Off-the-Shelf Solutions

1. The Robot Operating System’s Navigation library can be used for the autonomous navigation aspect of the walker’s functionality. [5]
2. Estimote Location Beacons from Estimote Inc. can be used for walker and user localization for indoor environments [4].
3. Several smart walker technologies already exist with features that have been considered or could be considered for Modern Mobility’s walker.
  a. Cornell engineering students developed a smart walker with electronic brakes and automatic braking when the user grabs the walker handgrips [1].
  b. Researchers at National Taiwan University created a smart walker named Johnnie that can autonomously navigate to the user. It also has a rehabilitation mode for helping the elderly to walk smoothly and safely [2].
  c. ETH Zurich created a smart walker called SmartWalker that can autonomously navigate to the user, and use electric motors to assists the user in walking. The pace of the walker adjusts to the user’s walking pace automatically [3].

## 3.3 Requirements Subject to Change

Table 4 - Requirements Subject to Change

Requirement | Justification
3.1.4, 1 | The Docking Station may not be necessary for charging, eliminating the need for this requirement.
3.1.4, 2 | The Docking Station may not be necessary for charging, eliminating the need for this requirement.
3.1.3, 10 | The phone app may not receive notifications if a request was failed.
3.2.2, 5 | Components have not yet been sourced and so what is a realistic final weight of the walker is not yet known.
3.3.3, 6 | A study of charging times of batteries feasible for this application has not yet been done.
3.3.3, 7 | This is an estimation; a more realistic requirement will be enforced upon further investigation.
3.3.3, 8 | A study of how much weight a standard walker can support has not been done.
3.3.4, 3 | The walker may ultimately not have an associated phone application at all. If it does, it could potentially be an iOS application as opposed to an Android. The requirement may also be extended to include both Android and iOS devices.

# Citations

[1] | “Engineers invent 'Smart Walkers' for elderly,” Phys.org - News and Articles on Science and Technology, 25-Jun-2010. [Online]. Available: https://phys.org/news/2010-06-smart-walkers-elderly.html. [Accessed: 31-Oct-2017].
[2] | Y. Kuan-Ting, “An Interactive Robotic Walker for Assisting Elderly Mobility in Senior Care Unit ,” IEEE, rep., 2010.
[3] | P. Ruegg, “A smart walking aid,” ETH Zurich, 26-Feb-2016. [Online]. Available: https://www.ethz.ch/content/main/en/news-und-veranstaltungen/eth-news/news/2016/02/smart-walker.html. [Accessed: 31-Oct-2017].
[4] | Estimote Inc. Available: https://estimote.com/
[5] | Navigation Stack. Robot Operating System. Available: http://wiki.ros.org/navigation

MODERN MOBILITY SMART WALKER SYSTEM REQUIREMENTS DOCUMENT Doc: SRD0001 Rev: B

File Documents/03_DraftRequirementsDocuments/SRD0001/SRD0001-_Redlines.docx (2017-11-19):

# SMART WALKER

# SYSTEM REQUIREMENTS DOCUMENT

MECHATRONICS 4TB6

GROUP 2

NATHAN FUJIMOTO

PRAKHAR GARG

JOSH GILMOUR

AARON JASS

TYLER JASS

FAUZIA KHANUM

JACK LIU

GAGAN SINGH

# Revision History

Rev | Author(s) | Description of Change | Peer Reviewed | Date
- | T.Jass | Original Document | A.Jass | 10-Oct-2017

A | N.Fujimoto P.Garg J.Gilmour A.Jass T.Jass F.Khanum J.Liu G.Singh | Original document was blank with just a layout. This revision adds content to the document. | N.Fujimoto P.Garg J.Gilmour A.Jass T.Jass F.Khanum J.Liu G.Singh | 01-Nov-2017

# Table of Tables

# Table of Figures

# 1 Introduction

## 1.1 Purpose

The standard medical walker or walking aid helps to improve stability and balance of its user while they are walking. The objective of this project is to modify a standard medical walker to include various mechanical and electrical components; autonomous features, in order to improve the user experience. The modified walker, called the SmartWalker, will involve designing and developing an autonomous and safe system while keeping all original functions of the standard medical walker.

This document defines the project scope, outlines the system overview and highlights the main functional and nonfunctional requirements of the SmartWalker.

## 1.2 Project Scope

The scope of this project is to design a walker with autonomous abilities to operate within a specific environment (refer to section 2.3 Operating Environment). The SmartWalker will feature:

- Autonomous driving between a ‘home’ location and the user within an indoor room, and vice-versa. The ‘home’ location is a docking station with charging capabilities.
- Autonomous obstacle avoidance when driving to and from the user.
- Assistive walking when using the SmartWalker normally, this includes assistive powering when going up ramps, and active braking when going down ramps.
- Emergency braking in any situation if approach a steep drop in elevation.
- Global Position System (GPS) tracking within the environment.

This project will not include (out of scope) the following items:

- Autonomous usage in multiple indoor environments, simultaneously (autonomous movement between multiple rooms).
  - Autonomous features in an entire hospital.
- Exact GPS tracking while walker is indoors.
- Wheelchair capabilities (primary seat usage, limited walking capabilities).

The end result of this project will demonstrate the students’ cumulative learning through their academic career via a demonstration of the SmartWalker’s autonomous ability in a predetermined location.

# 2 Overall Description

## 2.1 System Overview

The SmartWalker is an original idea by the Modern Mobility group, within the capstone course of the Computing and Software Department, 4TB6, at McMaster University. The focus of the SmartWalker project is to increase the utility of a standard medical walker by implementing various autonomous and electric features. Full system details and functionalities are explained below.

## 2.2 System Functionality

The SmartWalker has two main functionalities (or modes): autonomous mobility and manual driving.

- Autonomous Mobility: The ability to move out of the way of the user whenever requested to a designated home location as well as return to the user when requested.
- Manual Driving: The ability to operate like a standard medical walker, with added smart features like assisted braking and assisted driving.

These core functions are supported by two sub-functions: a smartphone application and a docking station. The smartphone application is used as an avenue to capture user-specific monitored variables, while the docking station is used to support the autonomous mobility function by acting as a home location.

## 2.3 Operating Environment

The operating environment of the SmartWalker is a typical hospital. This environment is divided into two areas: the patient’s room, and the hospital hallways/common rooms and outside grounds. Manual mode will be available in all environments (patient room, hospital corridors, hospital grounds etc.) while Autonomous mode will only be available in the patient room that contains its corresponding docking station.

Figure 1 below indicates a sample patient room in a hospital. The docking station would be located next to a wall plugged into an electrical outlet ready to charge the walker at any moment. The docking station will not be in the way of medical equipment and medical personnel such as doctors, nurses, and caregivers. Figure 2 below indicates a sample hospital and it’s surrounding outside grounds that the SmartWalker can be implemented in. [GPS CAPABILITY USING THE MAP, CAN’T SHOW FLOOR]

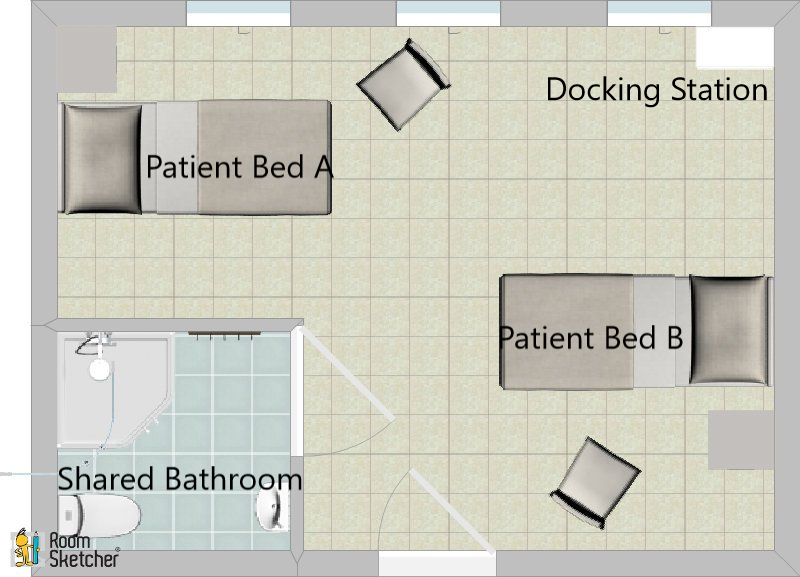
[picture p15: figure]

Figure 1 - Hospital Patient Room


Figure 2 - Google Maps Image of a Hospital and Surrounding Area

## 2.4 Assumptions and Dependencies

The following are the assumptions that we will be working with:

Environmental: The SmartWalker will be used in patient rooms that have enough room for wheelchairs to move about, therefore enough room for the SmartWalker to autonomously move about. It is assumed that the farthest the SmartWalker will be taken will the hospital grounds.

Functional: We will be using a structurally sound market walker as the basis for the SmartWalker. The SmartWalker battery will be charged via the docking station and no other method.

User Expectations: It is assumed the user of the SmartWalker has little experience interacting with technology such as smartphones and smartphone applications.

## 2.

## 5 Functional Decomposition and Variables

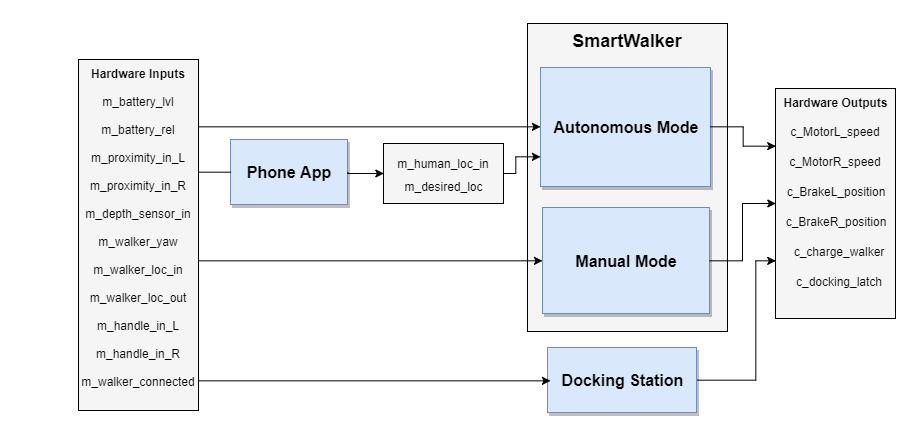
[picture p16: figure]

Figure 3 - Functional Decomposition Diagram

Table 1 - Monitored Variables

Variable | Description | Units | Range
m_battery_lvl | Power level of battery. | Battery Sustain of Charge (%) | [0, 100]
m_battery_rel | Reliability of the battery. | Battery Health (%) | [0, 100]
m_proximity_in_L | Proximity to any environment objects (front-left side). | Distance (m) | [0, 1]
m_proximity_in_R | Proximity to any environment objects (front-right side). | Distance (m) | [0, 1]
m_depth_sensor_in | Depth of the ground with respect to the walker. | Distance (m) | [-2, 0]
m_walker_yaw | Orientation of the walker (yaw) with respect to the walker’s z-axis. | Angle (deg) | [0, 360]
m_walker_loc_out | Global location of the walker. | [Longitude (deg), Latitude (deg)] | [-180, 180; -90,90]
m_walker_loc_in | Location of the walker inside the patient room, with respect to a preset coordinate system. | [x,y] on room map | Custom
m_human_loc_in | Location of the human based on their phone, with respect to a preset coordinate system. | [x, y] on room map | Custom
m_desired_loc | Desired location the user selects for the walker in autonomous mode. | Enum | GoDocking, GoHuman
m_handle_in_L | | Force (Nm)
m_handle_in_R

Table 2 - Controlled Variables

Variable | Type | Description | Units
c_motorL_speed | Controlled | Motor L speed | deg/s
c_motorR_speed | Controlled | Motor R speed | deg/s
c_brakeL_position | Controlled | Brake L position (engage, partially engaged, not engaged)
c_brakeR_position | Controlled | Brake R position (engaged, partially engaged, not engaged)
c_charge_walker | Controlled | Walker plugged in to charge | Boolean
c_docking_latch | Controlled | Walker latched at docked | Boolean

### 2.5.1 Autonomous Mode

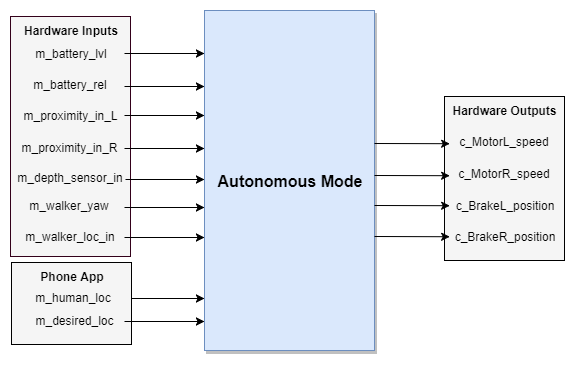
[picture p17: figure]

Figure 4 - Autonomous Mode Diagram

### 2.5.2 Manual Mode

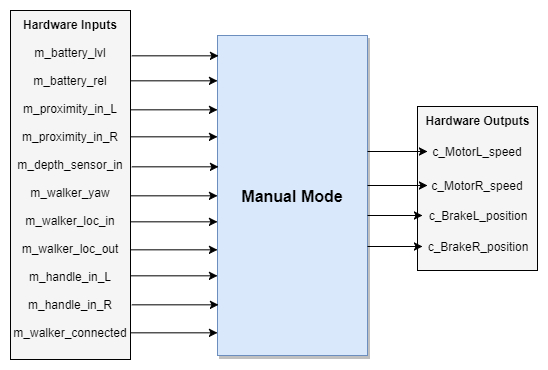
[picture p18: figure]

Figure 5 - Manual Mode Diagram

### 2.5.3 Phone App

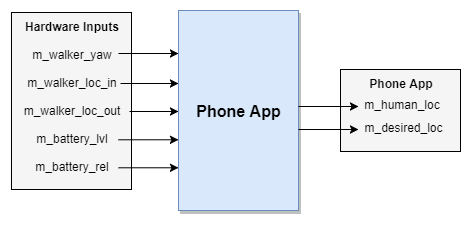
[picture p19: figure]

Figure 6 - Phone App Diagram

### 2.5.4 Docking Station

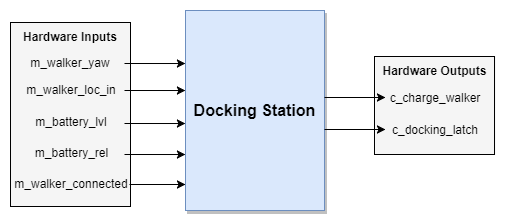
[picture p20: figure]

Figure 7 - Docking Station Diagram

# 3 Specific Requirements

## 3.1 Functional Requirements

### 3.1.1 Autonomous Mode

- Autonomous Mode shall not be possible if there is no power drawn from the onboard battery
- When requested via phone app, the SmartWalker shall navigate by itself to and from the user’s phone and docking station as per the request
- The SmartWalker shall detect obstructions in its path using proximity sensors
- The SmartWalker shall use a depth sensor to detect how far away objects/targets in its path are
- The SmartWalker shall receive its orientation and location information from an external source
- The SmartWalker shall receive the phone location and desired location from the phone app
- The SmartWalker shall obey the same drive/brake logic as specified in the Manual Mode section, however the hardware inputs will be replaced with software input commands

### 3.1.2 Manual Mode

- The SmartWalker shall have its <drive inputs> in the neutral state by default
- The SmartWalker’s left wheel shall be inactive and roll freely when the left-hand <drive input> is in its neutral state
- The SmartWalker’s left wheel shall be active and drive forward when the left-hand <drive input> is in its forward state
- The SmartWalker’s left wheel shall be active and drive backward when the left-hand <drive input> is in its backward state
- The SmartWalker’s right wheel shall be inactive and roll freely when the right-hand <drive input> is in its neutral state
- The SmartWalker’s right wheel shall be active and drive forward when the right-hand <drive input> is in its forward state
- The SmartWalker’s right wheel shall be active and drive backward when the right-hand <drive input> is in its backward state
- The SmartWalker’s linear speed shall be proportionally related to the deflection of the drive input that controls it
- The SmartWalker’s <drive inputs> shall not drive the motors if there is no power drawn from the onboard battery
- The SmartWalker shall have its brakes unapplied by default
- The SmartWalker shall decelerate and stop when the brakes are applied
- The SmartWalker shall allow its wheels to roll freely when the e-brake is in the released position
- The SmartWalker shall lock its wheels in place when the e-brake is in the unreleased position
- The SmartWalker shall detect the angle of the floor/ground beneath it
- The SmartWalker will detect a rapid change in elevation in its path

### 3.1.3 Phone App

- The phone application shall receive the SmartWalker’s orientation
- The phone application shall receive the SmartWalker’s location
- The Phone application shall receive the SmartWalker’s desired location
- The Phone application shall receive the battery’s reliability
- The Phone application shall receive the battery’s level
- The phone application shall communicate the user’s location to the SmartWalker
- The phone application shall communicate the desired location to the SmartWalker
- The Phone application shall communicate the battery’s reliability
- The Phone application shall communicate the battery’s level

### 3.1.4 Docking Station

- The docking station shall charge the on-board SmartWalker battery when it is docked
- The docking station shall lock in the SmartWalker when it is docked

### 3.1.5 Other Requirements

- The SmartWalker shall be defaulted to Manual Mode on startup
- The SmartWalker shall switch to Auto Mode when given an Auto Mode request
- The SmartWalker shall switch back to Manual Mode when the Auto Mode request is completed or failed
- The user shall turn the walker on or off using a <switch/button>
- The SmartWalker shall function as standard non-electric walker there is no power drawn from the onboard battery, or power is disabled

## 3.2 Non-Functional Requirements

3.2.1 Look and Feel Requirements

- The walker shall look as close to a standard walker as possible
- All functional components (electronics, motors) shall be enclosed and hidden from view

3.2.2 Usability requirements

- Braking shall be possible for those with physical ailments that limit the functionality and dexterity of their hands
- The walker shall be easily autonomously summoned by users with physical ailments that limit the functionality and dexterity of their hands
- Users not familiar with technology shall be able to learn to use the walker in under an hour
- The text size in any phone application can be varied by the user to aid those with poor eyesight
- The walker shall not weigh more than 150 pounds

3.3.3 Performance Requirements

- Speed requirements
  - It shall not take the walker more than five seconds to begin moving to it’s destination when the user commands the walker to come to them or return to the docking station
  - The walker’s digital user interface shall not take more than one second to respond to user input
  - When applied fully, the walker’s braking system shall bring the walker to a complete stop in a safe amount of time
- Safety critical requirements
  - The walker shall not run into people or objects while autonomously navigating
  - The walker shall not drive off of staircases while autonomously navigating
  - The walker shall not accelerate excessively while in use by the user
  - Moving components such as disk brakes, servo motors, and induction motors shall be enclosed to prevent injury
  - The moving component enclosures shall be tough enough that they do not sustain significant damage from minor impacts
- Precision requirements
  - The walker shall autonomously navigate into the docking station from any location in the room where there is a suitable path to the docking station
  - The walker shall eventually come within half a meter of the user after being commanded to navigate to the user when there is a suitable path
- Reliability and availability requirements
  - The walker shall take at most an hour to charge
  - On a full charge, the walker shall have enough battery for twenty minutes of standard usage
- Capacity requirements
  - The product shall be able to support the weight of a single user that weighs at most 300 pounds

3.3.4 Operational Requirements

- Expected physical environment
  - The walker is to be used by the elderly or mobility challenged individuals while standing up in an indoor, single-floor environment
  - The walker is to be used in environments where there are no doors between the walker and destinations the walker will be summoned too
- Expected technological environment
  - The walker must be able to interface with any modern android smartphone

3.3.5 Maintainability and Portability Requirements

- The application for communicating with the walker is expected to run on Android smartphones

3.3.6 Security Requirements

- Only registered caregivers, family, and significant others in a caregiving role shall be given the ability to use the GPS tracking feature of the walker

3.3.7 Legal Requirements

- GPS tracking functionality must be easily removed to facilitate sale in areas where such functionality is illegal or may become illegal
- As a medical device, the walker must meet Canada’s Medical Devices Regulations as outlined in SOR/98-282 http://laws-lois.justice.gc.ca/eng/regulations/SOR-98-282/index.html

3.3.8 Open Issues

- Investigation into the suitability of Google’s Eddystone technology for walker localization is not yet complete
- Investigation and testing of the suitability of using a single a Raspberry Pi for all system processing is not yet complete
- Investigation into whether the second version of the Microsoft Kinect is suitable for use with Linux and ROS is ongoing

3.3.9 Off-the-Shelf Solutions

- The ‘Robot Operating System’s’ Navigation library and it’s related libraries can be used for the autonomous navigation aspect
- Estimote Location Beacons from Estimote Inc. can be used for walker and user localization for indoor environments
  - Several other companies have similar technologies but Estimote Inc.’s product is what will likely be used
- Several smart walker technologies already exist with features that have been considered or could be considered for Modern Mobility’s walker
  - Cornell engineering students developed a smart walker with electronic brakes and automatic braking when the user grabs the walker handgrips [1].
  - Researchers at National Taiwan University created a smart walker named Johnnie that can autonomously navigate to the user. It also has a rehabilitation mode for helping the elderly to walk smoothly and safely
  - ETH Zurich created a smart walker called SmartWalker that can autonomously navigate to the user, and use electric motors to assists the user in walking. The pace of the walker adjusts to the user’s walking pace automatically.

# Citations

[1] | “Engineers invent 'Smart Walkers' for elderly,” Phys.org - News and Articles on Science and Technology, 25-Jun-2010. [Online]. Available: https://phys.org/news/2010-06-smart-walkers-elderly.html. [Accessed: 31-Oct-2017].
[2] | Y. Kuan-Ting, “An Interactive Robotic Walker for Assisting Elderly Mobility in Senior Care Unit ,” IEEE, rep., 2010.
[3] | P. Ruegg, “A smart walking aid,” ETH Zurich, 26-Feb-2016. [Online]. Available: https://www.ethz.ch/content/main/en/news-und-veranstaltungen/eth-news/news/2016/02/smart-walker.html. [Accessed: 31-Oct-2017].

MODERN MOBILITY SMART WALKER SYSTEM REQUIREMENTS DOCUMENT Doc: SRD0001 Rev: A

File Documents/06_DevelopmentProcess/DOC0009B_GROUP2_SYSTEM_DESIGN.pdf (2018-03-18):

MODERN MOBILITY
SMARTWALKER SYSTEM DESIGN
DOCUMENT

Doc: DOC0009
Rev: B

# SMART WALKER SYSTEM DESIGN DOCUMENT

MECHATRONICS 4TB6
GROUP 2
NATHAN FUJIMOTO | 1224348
PRAKHAR GARG | 1204351
JOSH GILMOUR | 1402325
AARON JASS | 1218859
TYLER JASS | 1218857
FAUZIA KHANUM | 1209252
JACK LIU | 1215056
GAGAN SINGH | 1306242

SMARTWALKER SYSTEM DESIGN
DOCUMENT

Rev: B

## Table of Contents

Table of Contents | 2
Table of Tables | 5
Table of Equations | 5
Table of Figures | 5
Revision History | 7
Purpose | 8
Scope | 8
1 Assumptions | 8
2 Context Diagram of Boundaries | 9
3 System Data Flow Diagram | 11
4 Monitored and Controlled Variables | 12
5 Constants | 15
6 Behaviour Overview | 17
6.1 Overall System Behaviour | 17
6.2 Navigation Goal Calculation | 20
7 Component Details | 22
8 Normal Operation | 26
8.1 Autonomous | 26
8.1.1 Moving to user | 26
8.1.2 Moving to docking station | 26
8.1.3 Docked | 27
8.2 Manual | 27
8.2.1 Regular Walking | 27
8.2.2 Slope Change | 27
8.2.3 Idle | 27
9 Undesired Event Handling | 29
9.1 Emergency Stop | 29
9.2 User Detected During Autonomous Mode | 29
9.3 Object Collision with Smartwalker | 29
9.4 Walker has Fallen Over or Very high Incline/Decline | 29
9.5 Goal location is unreachable | 30
9.6 Walker cannot “see” | 30
9.7 Walker is unable to move while autonomously navigating | 30
9.8 Extremely low battery | 30
10 System Overview | 31
11 Mechanical Components | 32
11.1 Walker | 32
11.2 Wheels | 32
11.3 Handles | 33
11.4 Sensor Mount | 33
12 Electrical Components | 34

SMARTWALKER SYSTEM DESIGN
DOCUMENT

Rev: B

12.1 Low Voltage Circuit | 34
12.1.1 Kinect | 35
12.1.2 Estimotes | 36
12.1.3 Motor Controller board | 36
12.1.4 Encoders | 36
12.1.5 Ultrasonic Sensors | 36
12.1.6 Potentiometers | 36
12.2 High Voltage | 36
12.2.1 Raspberry Pi 3B | 37
12.2.2 Motor Controller Board | 37
12.2.3 Arduino Micro | 37
12.2.4 Battery | 37
12.2.5 Power Distribution Board | 38
13 Software Components | 38
13.1 | Ultrasonic and Sensor Nodes | 39
13.1.1 | Purpose | 39
13.1.2 | Scope | 39
13.1.3 | Module Guideline | 40
13.1.4 | Module Interface Specification | 40
13.1.5 | Module Internal Design | 43
13.1.6 | Scheduling | 45
13.1.7 | Data Dictionary | 45
13.2 | Drive Module(s) | 46
13.2.1 | Purpose | 46
13.2.2 | Scope | 46
13.2.3 | Module Guideline | 47
13.2.4 | Module Interface Specification | 48
13.2.5 | Module Internal Design | 50
13.2.6 | Scheduling | 52
13.2.7 | Data Dictionary | 52
13.3 | Differential Drive Module | 53
13.3.1 | Purpose | 53
13.3.2 | Scope | 53
13.3.3 | Module Guideline | 53
13.3.4 | Module Interface Specification | 54
13.3.5 | Module Internal Design | 54
13.3.6 | Scheduling | 55
13.3.7 | Data Dictionary | 55
13.4 | Kinect Module | 56
13.4.1 | Purpose | 56
13.4.2 | Scope | 56
13.4.3 | Module Guideline | 56
13.4.4 | Module Interface Specification | 56

SMARTWALKER SYSTEM DESIGN
DOCUMENT

Rev: B

13.4.5 | Module Internal Design | 57
13.4.6 | Scheduling | 57
13.4.7 | Data Dictionary | 58
13.5 | Transform Module | 59
13.5.1 | Purpose | 59
13.5.2 | Scope | 59
13.5.3 | Module Guide | 59
13.5.4 | Module Interface Specification | 59
13.5.5 | Module Internal Design | 60
13.5.6 | Scheduling | 60
13.5.7 | Data Dictionary | 60
13.6 | HMI Module | 61
13.6.1 | Purpose | 61
13.6.2 | Scope | 61
13.6.3 | Module Guideline | 62
13.6.4 | Module Interface Specification | 62
13.6.5 | Module Internal Design | 64
13.6.6 | Schedule | 65
13.6.7 | Data Dictionary | 66
13.7 | Estimote Indoor SDK Module | 67
13.7.1 | Purpose | 67
13.7.2 | Scope | 67
13.7.3 | Module Guide | 67
13.7.4 | Module Interface Specification | 67
13.7.5 | Module Internal Design | 67
13.7.6 | Scheduling | 68
13.7.7 | Data Dictionary | 68
13.8 | move_base Module | 68
13.8.1 | Purpose | 68
13.8.2 | Scope | 68
13.8.3 | Module Guide | 69
13.8.4 | Module Interface Specification | 70
13.8.5 | Module Internal Design | 71
13.8.6 | Scheduling | 71
13.8.7 | Data Dictionary | 71
Appendix I | 74
References | 77

SMARTWALKER SYSTEM DESIGN
DOCUMENT

Rev: B

## Table of Tables

Table 1 - Entity Descriptions and Interactions | 10
Table 2 - Monitored Variables | 13
Table 3 - Controlled Variables | 14
Table 4 - Constants | 15
Table 5 - State Table | 18
Table 6 - Autonomous Mode States | 19
Table 7 - Manual Mode States | 21
Table 8 - Component Description | 24
Table 9 - Derived Timing Constraints | 24
Table 10 - Initialization | 25
Table 11 - Ultrasonic and Slider Publisher Decoding | 43
Table 12 - Conversion of Ultrasonic Measurement to Points | 44
Table 13 - Ultrasonic and Sensor Node Data Dictionary | 46
Table 14 - Velocity Selection Calculation | 51
Table 15 - Drive Module Data Dictionary | 52
Table 16 - Differential Drive Data Dictionary | 55
Table 17 - move_base Data Dictionary | 73

## Table of Equations

Equation 1 - Navigation Goal Calculation | 20
Equation 2 - Ultrasonic and Slider Publisher Decoding | 43
Equation 3 - Calculating Magnitude from Ultrasonic Sensors | 45

## Table of Figures

Figure 1 - Context Diagram of Boundaries | 9
Figure 2 - System Data Flow Diagram | 11
Figure 3 - Kinect and Ultrasonic Orientation | 16
Figure 4 - Overall System Behaviour Diagram | 17
Figure 5 - Autonomous Mode Behaviour Diagram | 18
Figure 6 - Manual Mode Behaviour Diagram | 20
Figure 7 - Electrical Component Diagram | 22
Figure 8 - System Component Breakdown | 31
Figure 9 - Low Voltage Circuit | 35
Figure 10 - High Voltage Circuit | 37
Figure 11 - Software System Map | 39
Figure 12 - Ultrasonic and Sensors Node Guideline | 40

SMARTWALKER SYSTEM DESIGN
DOCUMENT

Rev: B

Figure 13 - Drive Module Guideline | 47
Figure 14 - Differential Drive Module Guideline | 53
Figure 15 - Kinect Module Guideline | 56
Figure 16 - Transform Node Module Guideline | 59
Figure 17 - HMI Module Guideline | 62
Figure 18 - Estimote Indoor SDK Module Guideline | 67
Figure 19 - move_base Module Guideline | 69

SMARTWALKER SYSTEM DESIGN
DOCUMENT

Rev: B

## Revision History

Rev | Author(s) | Description of Change | Peer Reviewed | Date
- | F.Khanum | Original Document (Copy of System Design Rev 0) | T.Jass | 07-Mar-2018
A | T.Jass | Merged in content from Component Design Rev 0 Made several comments and edits based on TA Feedback | T.Jass | 12-Mar-2018
B | T.Jass | Finalized Edits and additions | A.Jass | 16-Mar-2018

SMARTWALKER SYSTEM DESIGN
DOCUMENT

Rev: B

## Purpose

This document’s purpose is to define and portray the overall system design of all the SmartWalker capstone project. The designs in this document considers all system requirements, defined in the SmartWalker System Requirements document. The document will communicate all the necessary designs for each functional component of the SmartWalker. By the end, the reader should have a clear understanding of what each component is, and how its design meets and satisfies the requirements. The System Design document will be used to begin implementation of the SmartWalker.

## Scope

The scope of this project is to design a walker with autonomous abilities to operate within a specific environment. It is assumed the SmartWalker will be operating in a single room with level floors. Most likely it would be a patient’s room in a hospital. This document also includes the specification of the system’s complete component design. It is intended to give as much detail per component to be able to properly create each component without doubt. All specifications and constraints are labelled clearly for easier reference later when the team reaches the verification and validation stage of the project.
This project will include (in scope) the following items:
- Autonomous driving (see section 8.1 Autonomous for details) between the user and docking station within one indoor room at a time. The docking station is a temporary storage location with charging capabilities.
- Obstacle avoidance in Autonomous mode.
- Motor and brake controls available to the user while the SmartWalker is in Manual mode. This project will not include (out of scope) the following items:
- Autonomous usage in multiple indoor rooms simultaneously (autonomous movement is limited to one room).
- Global Positioning system (GPS) tracking
- Development of the docking station due to time and budget constraints, however, we will describe its functionality for context and use on its role with the SmartWalker.
The end result of this project will demonstrate the students’ cumulative learning through their academic career via a demonstration of the SmartWalker’s autonomous ability in a predetermined location. The SmartWalker herein referred to as walker.

## 1 Assumptions

1. The SmartWalker is designed to be used in a single room (likely the room of a hospital patient)
2. The ceiling and walls are mostly a light shade (beige, light grey, white, etc) and homogenous
3. The floor is expected to be relatively flat (subtle ramps are acceptable but no steps or steep slopes)
4. No clothing, debris, or other possible obstructions are in the way of sensors

SMARTWALKER SYSTEM DESIGN
DOCUMENT

Rev: B

## 2 Context Diagram of Boundaries

The System Context Diagram gives a high-level overview of the information passed to the major system components. The entities and interactions between them are described in Table 1 - Entity Descriptions and Interactions. More detailed information can be seen in Section 3 System Data Flow Diagram.

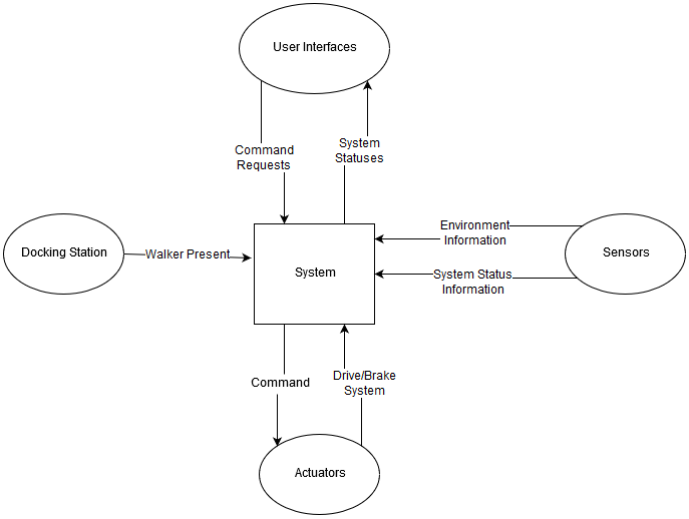
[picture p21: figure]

Figure 1 - Context Diagram of Boundaries

SMARTWALKER SYSTEM DESIGN
DOCUMENT

Rev: B

Entities | Entity Description | Entity Interactions | Interaction Description
System | The core of all operations. The "system" manages all of the information, computes required information, and outputs information needed by other entities. | See rows below
User Interfaces | These are the components that the user uses to interact with the system, this would include the phone application and the on-board touch screen. | ● Request to navigate autonomously (to user/target location/docking station) ● Request to drive manually ● Request to stop moving | ● SmartWalker location (at the dock, at the user, in transit) ● SmartWalker behavioural state (idle, navigating autonomously, driving manually)
Docking Station | The docking station is the walker's "Home", it is where it goes to charge. | The Docking Station functionality is no longer in scope for this project
Actuators | Components that execute a physical action. This would include the system's motors. | ● Requests to actuate (drive/stop motors) | ● Actuator statuses are provided by sensors
Sensors | Components that monitor and measure environment or internal information. This information would include the system's camera vision sensor, proximity sensors, and encoders. | ● Requests for SmartWalker environment data (such as object proximity) ● Requests for actuator state/performance (such as motor position) | ● Requested environment data ● Requested actuator data

Table 1 - Entity Descriptions and Interactions

SMARTWALKER SYSTEM DESIGN
DOCUMENT

Rev: B

## 3 System Data Flow Diagram

The system Data Flow diagram shows how the different components of the system interact with each other, and with their respective inputs and outputs. The centre of all operations is the Raspberry Pi, which is effectively both the brain and the lesion controlling the flow of all information going in and out of the system.

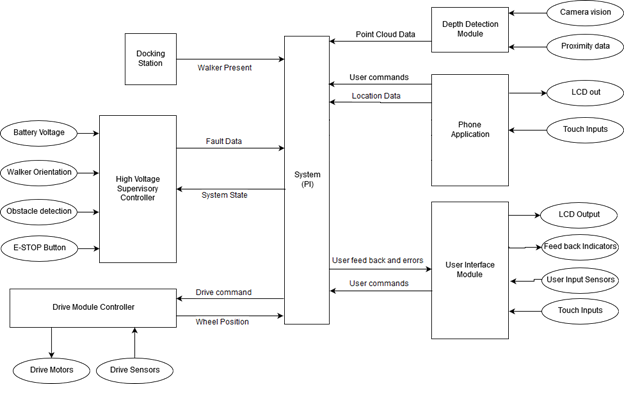
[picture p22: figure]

Figure 2 - System Data Flow Diagram

SMARTWALKER SYSTEM DESIGN
DOCUMENT

Rev: B

## 4 Monitored and Controlled Variables

Variable | Description | Units | Range
m_proximity_in_L | Proximity to any objects in the environment (front-left side). | Distance (cm) | [0, 500]
m_proximity_in_R | Proximity to objects in the environment (front-right side). | Distance (cm) | [0, 500]
m_depth_in | Depth of the upcoming ground with respect to the bottom of the walker. | Distance (cm) | [-100, 0]
m_walker_yaw | Orientation of the walker (yaw) with respect to the walker’s z-axis. | Angle (deg) | [-180, 180]
m_walker_pitch | Orientation of the walker (pitch) with respect to the walker’s y-axis. | Angle (deg) | [-45, 45]
m_walker_loc_out | Global location of the walker. | [Longitude (deg), Latitude (deg)] | [-180, 180; -90,90]
m_walker_loc_in | Location of the walker inside the patient room, with respect to a preset coordinate system. | [x,y] on room map | [0, 100; 0, 100]
m_human_loc_in | Location of the human based on their phone, with respect to a preset coordinate system. | [x, y] on room map | [0, 100; 0, 100]
m_human_yaw | Orientation of the human (yaw) about the human’s z-axis. | Angle (deg) | [-45, 45]

SMARTWALKER SYSTEM DESIGN
DOCUMENT

Rev: B

m_desired_loc | User selected desired location for the walker in autonomous mode | Enum (states) | GoDocking, GoHuman
m_dock_aligned | Walker is physically aligned with the docking station | Boolean | 0, 1
m_user_in_L | Desired forward assisted movement for the user, for the left motor. | Custom | [-100,100]
m_user_in_R | Desired forward assisted movement for the user, for the left motor. | Custom | [-100,100]
m_emergency_signal | Signal for monitoring an emergency situation. | Boolean | 0, 1

Table 2 - Monitored Variables

SMARTWALKER SYSTEM DESIGN
DOCUMENT

Rev: B

Variable | Description | Units | Range
c_motorL_speed | Left motor speed. | Angular velocity ( deg/s) | [0, 50]
c_motorR_speed | Right motor speed. | Angular velocity (deg/s) | [0, 50]
c_brakeL_position | Left brake position. | Brake Position (%) | [0, 100]
c_brakeR_position | Right brake position. | Brake Position (%) | [0, 100]
c_charge_walker | Charge the walker. | Boolean | 0, 1
c_dock_connected | Walker physically connected to the docking station. | Boolean | 0, 1

Table 3 - Controlled Variables

SMARTWALKER SYSTEM DESIGN
DOCUMENT

Rev: B

## 5 Constants

Number | Description | Value
1 | Number of Kinect Sensors | 1
2 | Location and orientation of Kinect sensors | Refer to Figure 3 -Kinect and Ultrasonic Orientation
3 | Number of ultrasound sensors | 4
4 | Location and orientation of ultrasound sensors | Refer to Figure 3 -Kinect and Ultrasonic Orientation
5 | PID Coefficients | (Kp, Ki, Kd) = To be determined
6 | SmartWalker Input Voltage | 12 Volts
7 | Number of Arduinos | 3
8 | Number of Raspberry Pis | 2
9 | Number of Motor Actuated Wheels | 2
10 | Number of Motor Control boards | 1
11 | Number of encoders (quadrature) | 2
12 | SmartWalker maximum speed when in autonomous mode | 1 meters/second
13 | SmartWalker maximum speed in manual mode | 1 meters/second ???
14 | Minimum allowable distance to objects in the environment during autonomous navigation | 0.25 meters
15 | Distance from target position the SmartWalker should stop at after autonomous navigation | 0.25 meters

Table 4 - Constants

SMARTWALKER SYSTEM DESIGN
DOCUMENT

Rev: B

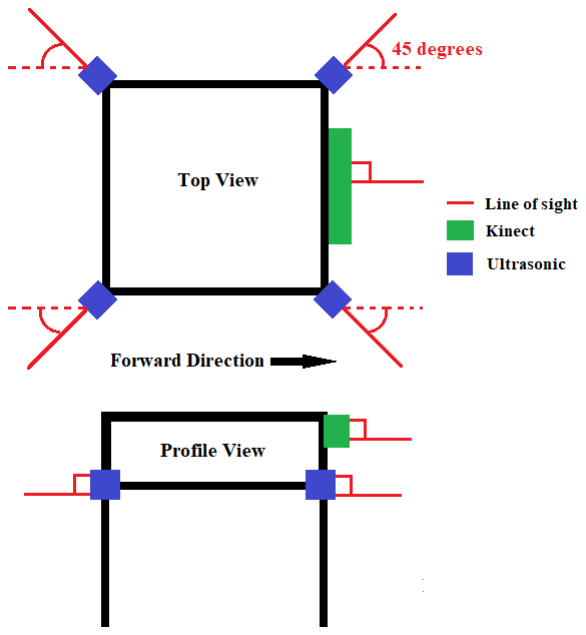
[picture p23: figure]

Figure 3 - Kinect and Ultrasonic Orientation

SMARTWALKER SYSTEM DESIGN
DOCUMENT

Rev: B

## 6 Behaviour Overview

### 6.1 Overall System Behaviour

The behaviour of the walker system can be seen by the following behavioural state diagrams. To describe at the main behavioural components of the walker system, three state diagrams were outlined: the overall system behaviour diagram, the autonomous behaviour diagram, and the manual mode behaviour diagram. The latter two main sub states in which the walker primarily operates in. In any state, the walker is perceiving information from the environment for both functioning and state transitioning.

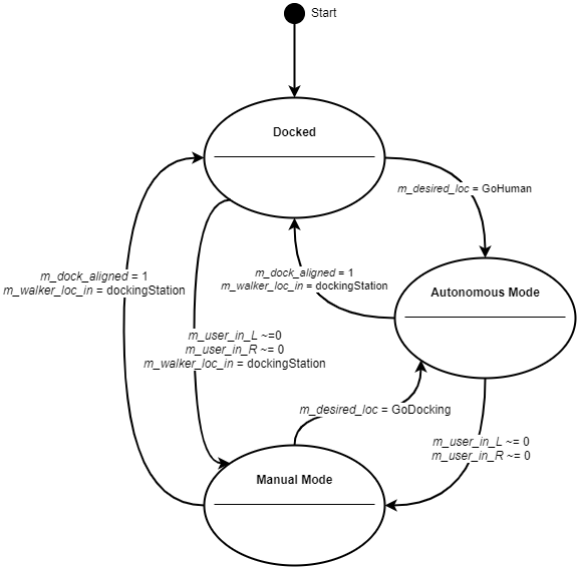
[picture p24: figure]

Figure 4 - Overall System Behaviour Diagram

SMARTWALKER SYSTEM DESIGN
DOCUMENT

Rev: B

State | Description
Docked | In this state the walker is physically connected to the docking station. When connected, the walker is charging its onboard power supply.
Autonomous Mode | In this state the walker is autonomously navigating to and from the user and the docking station (or its current position).
Manual Mode | In this state the walker is being manually operated by the user. This is intended as standard walker usage, with additional safety features.

Table 5 - State Table


Figure 5 - Autonomous Mode Behaviour Diagram

Please note, whenever the walker is put into an unintended event, a safety check will be done of the status of the system, and the status will be fixed if possible and sent back to the idle position.

SMARTWALKER SYSTEM DESIGN
DOCUMENT

Rev: B

State | Description
Idle | In this state the walker is in a waiting phase where it is waiting on instructions on where to navigate by the user, via the user interface.
Find Walker Pose | In this state the walker determines its relative position on the constructed map grid, as well as its relative yaw angle on the map.
Find User Pose | In this state the walker system determines the relative position of the user on the constructed map grid, as well as the user’s relative yaw angle on the map.
Navigate to Goal | In this state, considering the walker pose and user pose, the walker calculates the navigation goal and thus begins to navigate to the location.
Determine Distance to Advance | In this state the walker determines how far it can safely approach the destination.
Reverse Walker Orientation | In this state the walker orientates its yaw relative yaw angle so that its handles are facing the user (180-degree turn).
Move Distance Towards User | In this state the walker creeps until it has reached the safe approaching distance. The system then goes back to the idle state.

Table 6 - Autonomous Mode States

As described in the overall system behaviour diagram, if either the walker has reached the docking station or the user physically interacts with walker will the behaviour exit the autonomous mode.

SMARTWALKER SYSTEM DESIGN
DOCUMENT

Rev: B

### 6.2 Navigation Goal Calculation

The walker and user pose will both be determined by the beacons in the room. The goal is the location where the robot is supposed to travel based on where the user is. The goal is calculated to be some distance, K, in front of the user. It is calculated as:

Equation 1 - Navigation Goal Calculation

The pi added to the user orientation ensures that the walker is facing the user at the end of navigation. This facilitates the measurement of distance between the walker and user in the next state. The walker is then to turn around and approach the user to a reasonable distance (to be determined).


Figure 6 - Manual Mode Behaviour Diagram

SMARTWALKER SYSTEM DESIGN
DOCUMENT

Rev: B

State | Description
Idle | In this state the walker is in a waiting phase where it awaits physical interaction from the user, in the form of the handle sliders being moved.
Check if Walker is Safe | In this state the walker immediately checks the environment if there are any detectable dangerous obstacles or landmarks in the vicinity of the walker.
Walker in Use | Once the system deems it is safe, in this state the walker operates like a traditional walker, where it helps the user move him or herself.
Emergency Detected | In this state an emergency was detected and the walker brakes so it cannot be further moved. A safety check is completed so the emergency situation is no longer present.

Table 7 - Manual Mode States

Please note, the Emergency Detected includes the detection of any hazardous situations the user is in the vicinity of (oncoming drops, large slopes, etc..). The safety check will enact functionality to aid the user if wished to proceed through the hazard, if possible (please refer to Section 8 Normal Operation) Manual mode behaviour is left when the user asks for the walker to navigate back to the docking station, or to a new position where the user would be.

SMARTWALKER SYSTEM DESIGN
DOCUMENT

Rev: B

## 7 Component Details


Figure 7 - Electrical Component Diagram

SMARTWALKER SYSTEM DESIGN
DOCUMENT

Rev: B

Component | Inputs | Outputs | Description
Raspberry Pi | Modules: ● Microsoft Kinect ● Estimotes ● Android Mobile Phone | Modules: ● Drive Module Left ● Drive Module Right ● Human Interface Module | The main supervisory module in the walker System. It directs data to and from the other modules to assure functionality.
Estimotes | Monitored Variables: ● m_walker_loc_in | Modules: ● Raspberry Pi | Wireless beacons to be used for indoor location and navigation of the walker System.
Android Phone | Monitored Variables: ● m_human_loc_in ● m_human_yaw ● m_desired_loc | Modules: ● Raspberry Pi | The assumed personal electronic device that is owned by the user. This device will host the walker Application that will transmit commands and user location information, and receive system system status information.
Kinect (Sensory Module) | Monitored Variables: ● m_proximity_in_L ● m_proximity_in_R ● m_depth_in ● m_walker_yaw ● m_walker_pitch | Modules: ● Raspberry Pi | Sensor returning point cloud data about the environment. This sensor is vital to the system’s object detection.
Drive Modules | Modules: ● Raspberry Pi ● Human Interface Module | Control Variables: ● c_motorL_speed ● c_motorR_speed ● c_brakeL_position ● c_brakeR_positio n | Modules that will do computations on the internal system data and external environment data from the sensors and use it to control the actuators (motors) appropriately.
Human Interface | Monitored Variables: ● m_user_in_L | Modules: ● Drive Modules | This module is the physical interface between the

SMARTWALKER SYSTEM DESIGN
DOCUMENT

Rev: B

Module | ● m_user_in_R ● m_emergency_sig nal Modules: ● Raspberry Pi

drive module and the
user. It allows the user to manually drive the walker
system’s motors.

Table 8 - Component Description

Module | Derive Timing Constraints
Kinect | Cannot read data from the Kinect faster than the Raspberry Pi can process it whilst also maintaining other system functionality
Android Phone | Will communicate messages from the user at the standard Bluetooth 4.0 speeds to the Raspberry Pi (on the walker), and back to the user.
Estimotes | The beacon responsiveness will adhere to the Raspberry Pi’s scanning of the beacons while in Autonomous Mode.
Raspberry Pi | Must communicate with the arduinos at a rate they can handle and are configured to accept.
Drive Modules | Arduinos must communicate with the Pi and motor controllers at a rate they can handle and are configured to accept. The arduinos must run fast enough that it does not miss any encoder counts and are able to keep up with the rate of them.
Human Interface Module | The status of the human and environment interactions must be checked often enough that no user interactions are missed. Braking inputs and ultrasonic data will adhere to serial ‘I-squared-C’ speeds for sending data to the Raspberry Pi and to the Drive Modules.

Table 9 - Derived Timing Constraints

SMARTWALKER SYSTEM DESIGN
DOCUMENT

Rev: B

Module | Initialization
Kinect | Run the libfreenect driver to allow reading data from the Kinect.
Android Phone | The app must be running on the phone and a bluetooth connection established with the walker before several walker features can be used, such as autonomous navigation.
Estimotes | Physically the beacons required to be on the walls of the room, at the centre of each wall. Additionally, one would have to be inside the walker and connected to the Raspberry Pi at initialization.
Raspberry Pi | The Raspberry Pi will be turned on and have the necessary software pre-installed.
Drive Modules | The Arduinos, motor controllers, motors, and encoders will all have to be turned on via power-up. The arduinos will have the necessary software pre-installed.
Human Interface Module | The arduino and the sensors to interact with the human and environment (brakes and ultrasonic) will be initialized at power-up.

Table 10 - Initialization

SMARTWALKER SYSTEM DESIGN
DOCUMENT

Rev: B

## 8 Normal Operation

The following section will describe the different modes and states each mode has in more detail by stepping through possible positive normal scenarios.

Please note since this is the Draft System Design that we have not determined all details yet and have noted said details to be defined later.

### 8.1 Autonomous

As mentioned in our System Requirements document, autonomous mode is the ability to move out to a designated home location as well as return to the user when requested. Autonomous mode consists 3 states: moving to user, moving to docking station, and docked. The following sections will describe positive normal scenarios (behaviour the system should cover and everything proceeds as expected).

### 8.1.1 Moving to user

1. User is not detected by handlebar sensors (m_user_in_L and m_user_in_R)
2. User requests the walker to come to user via phone app
3. Phone app sends bluetooth signal to walker
4. If walker is not within bluetooth distance?
a. Display message to user “Walker out of reach.”
5. If walker is within bluetooth distance
a. Walker retrieves walker pose from estimotes
b. Walker retrieves user pose from estimotes
c. Walker calculates the goal pose and begins navigating to it, as described before
d. Once the walker reaches the goal, the distance to the user is measured
e. The walker turns 180 degrees
f. The walker backs up to within a reasonable distance from the user
g. Walker returns to idle state

### 8.1.2 Moving to docking station

1. User is not detected by handlebar sensors (m_user_in_L and m_user_in_R)
2. User sends signal to dock via phone app
3. If walker is not within bluetooth distance
a. Display message to user “Walker out of reach.”
4. If walker is within bluetooth distance
h. Walker retrieves walker pose from estimotes
i. Walker retrieves docking station pose from estimotes
j. Walker moves to docking station
k. Walker docks into charging port (m_dock_aligned)
i. Go to Docked state

SMARTWALKER SYSTEM DESIGN
DOCUMENT

Rev: B

### 8.1.3 Docked

1. Walker is at the docking station and connected (c_dock_connected)
a. If battery is less than 100% (m_battery_lvl)
1. charge (c_charge_walker)
ii. If battery is at 100% (m_battery_lvl)
1. Disengage charging and go to Idle state

### 8.2 Manual

As mentioned in our System Requirements document, Manual mode is the ability to operate like a standard medical walker, with added smart features such as assisted braking and assisted driving. Manual mode has 4 states: regular walking, slope change, objects detected, and idle. The following sections will describe positive normal scenarios (behaviour the system should cover and everything proceeds as expected).

### 8.2.1 Regular Walking

This state is when the user is utilizing the walker as intended; aiding in regular walking.

1. User detected at handlebar sensors (m_user_in_L and m_user_in_R)
a. Detect if the walker is moving and surrounding environment
i. Slope change → Slope Change mode
ii. | Objects in way → Objects detected
iii. | User is utilizing walker for normal walking
b. User applies brakes manually (c_brakeL_position and c_brakeR_position)
i. reduce speed accordingly
2. If user is not detected (for more than a certain amount of time, to be determined)
a. Enter idle state

### 8.2.2 Slope Change

This state is for when the user is detected at the handlebar sensors, the user is walking around with the aid of the walker and the smartwalker has detected a change in slope of the ground.

1. Query the slope of the ground using the onboard sensors
2. Calculate the pitch of the walker (m_walker_pitch)
3. If the pitch of the walker is positive or negative 5 deg to a certain deg
a. This state has yet to be finalized, more details to come in the future

### 8.2.3 Idle

1. User is not detected at handlebar sensors (m_user_in_L and m_user_in_R)
a. If walker is not detected at docking station (m_dock_aligned)

SMARTWALKER SYSTEM DESIGN
DOCUMENT

Rev: B

- Walker waits for command from user
b. If walker is detected at docking station (m_dock_aligned)
- If battery is less than 100% (m_battery_lvl)
- charge walker (c_charge_walker)
- If battery is 100% (m_battery_lvl)
- Sit idle (details of idle mode to be determined)

SMARTWALKER SYSTEM DESIGN
DOCUMENT

Rev: B

## 9 Undesired Event Handling

Section 7 covered normal operation of the walker, this section will talk about abnormal scenarios and how the walker will handle them. Each section will describe the undesired event and the steps the system will take to ensure that the event is resolved in a safe manner.
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

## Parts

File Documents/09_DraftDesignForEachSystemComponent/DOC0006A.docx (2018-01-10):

# DRAFT SYSTEM DESIGN

# DOCUMENT

MECHATRONICS 4TB6

GROUP 2

NATHAN FUJIMOTO

PRAKHAR GARG

JOSH GILMOUR

AARON JASS

TYLER JASS

FAUZIA KHANUM

JACK LIU

GAGAN SINGH

# Table of Contents

# Table of Figures

No table of figures entries found.

# Table of Tables

No table of figures entries found.

# Revision History

Rev | Author(s) | Description of Change | Peer Reviewed | Date
- | T.Jass | Original Document | | 05-Jan-2017
A

# Purpose

# Scope

MODERN MOBILITY DRAFT SYSTEM DESIGN DOCUMENT Doc: DOC0006 Rev: A

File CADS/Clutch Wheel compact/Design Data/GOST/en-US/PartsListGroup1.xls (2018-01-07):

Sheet: Лист 1
Инв. № подл |  |  |  | Подп. и дата | Взам. инв. № | Инв. № дубл. |  |  | Подп. и дата
Формат | Зона | Поз. | Обозначение |  |  |  | Наименование |  |  |  |  |  | Кол. на исполнение
 |  |  |  |  |  |  |  |  |  |  |  | Лит.
 |  |  |  |  |  |  |  |  |  |  |  | Код
 |  |  |  |  |  |  |  | Изм. | Лист | № докум | Подпись |  | Дата
 |  |  |  |  |  |  |  | Разраб.
 |  |  |  |  |  |  |  | Пров.
 |  |  |  |  |  |  |  | Н.контр
 |  |  |  |  |  |  |  | Утв.
 |  |  |  |  |  |  |  |  |  |  |  |  |  | Копировал

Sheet: Лист 2
Инв. № подл |  |  |  | Подп. и дата | Взам. инв. № | Инв. № дубл. |  |  | Подп. и дата
Формат | Зона | Поз. | Обозначение |  |  |  | Наименование |  |  |  |  | Кол. на исполнение
 |  |  |  |  |  |  |  | Изм. | Лист | № докум. | Подп. | Дата
 |  |  |  |  |  |  |  |  |  |  |  |  | Копировал
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

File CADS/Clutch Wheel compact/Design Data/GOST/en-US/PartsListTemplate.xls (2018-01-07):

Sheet: Лист 1
 | Формат | Зона |  | Поз. |  | Обозначение |  |  |  | Наименование |  |  |  | Кол. | Приме-чание
Подп. и дата
Инв. № дубл.
Взам. инв. №
Подп. и дата
 | Изм. |  | Лист |  | № докум |  | Подпись | Дата
Инв. № подл | Разраб. |  |  |  |  |  |  |  |  |  | Литера |  | Лист |  |  | Листов
 | Пров.
 | Н.контр
 | Утв.
 |  |  |  |  |  |  |  |  | Копировал |  |  | Формат А4

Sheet: Лист 2
 | Формат | Зона |  | Поз. |  | Обозначение |  |  |  | Наименование |  | Кол. | Приме-чание
Подп. и дата
Инв. № дубл.
Взам. инв. №
Подп. и дата
Инв. № подл
 | Изм. |  | Лист |  | № докум. |  | Подп. |  | Дата
 |  |  |  |  |  |  |  | Копировал |  |  | Формат А4
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

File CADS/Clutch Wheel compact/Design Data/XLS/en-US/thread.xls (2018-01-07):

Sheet: Inch Tapping Threads
I Q X | Inch Tapping Threads |  | Sort Order - 5 |  | External |  |  |  |  |  |  | Internal
 |  |  |  |  |  | Major Dia |  | Pitch Dia |  | Minor Dia |  |  | Minor Dia |  | Pitch Dia |  | Major Dia |  | Tap Drill
Size | Size Suffix | Thread Designation | Custom Thread Designation | TPI | Class | Max | Min | Max | Min | Max | Min | Class | Min | Max | Min | Max | Min | Max | Basic
0.0600 |  | 0-48 | 0-48 | 48 | 2B | 0.0600 | 0.0540 | 0.0480 | 0.0435 | 0.0360 | 0.0330
0.0730 |  | 1-42 | 1-42 | 42 | 2B | 0.0750 | 0.0690 | 0.0620 | 0.0575 | 0.0490 | 0.0460
0.0860 |  | 2-32 | 2-32 | 32 | 2B | 0.0880 | 0.0820 | 0.0760 | 0.0710 | 0.0640 | 0.0600
0.0990 |  | 3-28 | 3-28 | 28 | 2B | 0.1010 | 0.0950 | 0.0880 | 0.0830 | 0.0750 | 0.0710
0.1120 |  | 4-24 | 4-24 | 24 | 2B | 0.1140 | 0.1080 | 0.1000 | 0.0950 | 0.0860 | 0.0820
0.1250 |  | 5-20 | 5-20 | 20 | 2B | 0.1300 | 0.1230 | 0.1120 | 0.1065 | 0.0940 | 0.0900
0.1380 |  | 6-20 | 6-20 | 20 | 2B | 0.1390 | 0.1320 | 0.1215 | 0.1155 | 0.1040 | 0.0990
0.1510 |  | 7-19 | 7-19 | 19 | 2B | 0.1540 | 0.1470 | 0.1345 | 0.1280 | 0.1150 | 0.1090
0.1640 |  | 8-18 | 8-18 | 18 | 2B | 0.1660 | 0.1590 | 0.1440 | 0.1375 | 0.1220 | 0.1160
0.1900 |  | 10-16 | 10-16 | 16 | 2B | 0.1890 | 0.1820 | 0.1650 | 0.1585 | 0.1410 | 0.1350
0.2160 |  | 12-14 | 12-14 | 14 | 2B | 0.2150 | 0.2080 | 0.1895 | 0.1825 | 0.1640 | 0.1570
0.2420 |  | 14-14 | 14-14 | 14 | 2B | 0.2410 | 0.2340 | 0.2130 | 0.2060 | 0.1850 | 0.1780
0.2500 |  | 1/4-14 | 1/4-14 | 14 | 2B | 0.2460 | 0.2370 | 0.2190 | 0.2110 | 0.1920 | 0.1850
0.3125 |  | 5/16-12 | 5/16-12 | 12 | 2B | 0.3150 | 0.3060 | 0.2795 | 0.2710 | 0.2440 | 0.2360
0.3750 |  | 3/8-12 | 3/8-12 | 12 | 2B | 0.3800 | 0.3710 | 0.3445 | 0.3350 | 0.3090 | 0.2990
0.4375 |  | 7/16-10 | 7/16-10 | 10 | 2B | 0.4400 | 0.4290 | 0.3995 | 0.3890 | 0.3590 | 0.3490
0.5000 |  | 1/2-10 | 1/2-10 | 10 | 2B | 0.5040 | 0.4930 | 0.4635 | 0.4530 | 0.4230 | 0.4130

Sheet: Metric Forming Screw Threads
M P X | Metric Forming Screw Threads |  | Sort Order - 6 |  | External |  |  |  |  |  |  | Internal
 |  |  |  |  |  | Major Dia |  | Pitch Dia |  | Minor Dia |  |  | Minor Dia |  | Pitch Dia |  | Major Dia |  | Tap Drill
Size | Size Suffix | Thread Designation | Custom Thread Designation | Pitch | Class | Max | Min | Max | Min | Max | Min | Class | Min | Max | Min | Max | Min | Max | Basic
1.5 |  | 1.5x0.5 | 1.5x0.5 | 0.5 | 6g | 1.520 | 1.380 | 1.215 | 1.110 | 0.910 | 0.840
1.5 |  | ST1.5x0.5 | ST1.5x0.5 | 0.5 | 6g | 1.520 | 1.380 | 1.215 | 1.110 | 0.910 | 0.840
1.9 |  | 1.9x0.6 | 1.9x0.6 | 0.6 | 6g | 1.900 | 1.760 | 1.570 | 1.465 | 1.240 | 1.170
1.9 |  | ST1.9x0.6 | ST1.9x0.6 | 0.6 | 6g | 1.900 | 1.760 | 1.570 | 1.465 | 1.240 | 1.170
2.2 |  | 2.2x0.8 | 2.2x0.8 | 0.8 | 6g | 2.240 | 2.100 | 1.935 | 1.810 | 1.630 | 1.520
2.2 |  | ST2.2x0.8 | ST2.2x0.8 | 0.8 | 6g | 2.240 | 2.100 | 1.935 | 1.810 | 1.630 | 1.520
2.6 |  | 2.6x0.9 | 2.6x0.9 | 0.9 | 6g | 2.570 | 2.430 | 2.235 | 2.115 | 1.900 | 1.800
2.6 |  | ST2.6x0.9 | ST2.6x0.9 | 0.9 | 6g | 2.570 | 2.430 | 2.235 | 2.115 | 1.900 | 1.800
2.9 |  | 2.9x1 | 2.9x1 | 1 | 6g | 2.900 | 2.760 | 2.540 | 2.420 | 2.180 | 2.080
2.9 |  | 2.9x1.1 | 2.9x1.1 | 1.1 | 6g | 2.900 | 2.760 | 2.540 | 2.420 | 2.180 | 2.080
2.9 |  | ST2.9x1.1 | ST2.9x1.1 | 1.1 | 6g | 2.900 | 2.760 | 2.540 | 2.420 | 2.180 | 2.080
2.9 |  | 2.9x1.3 | 2.9x1.3 | 1.3 | 6g | 2.900 | 2.720 | 2.540 | 2.355 | 1.890 | 1.700
2.9 |  | 2.9x1.4 | 2.9x1.4 | 1.4 | 6g | 2.900 | 2.720 | 2.340 | 2.175 | 1.780 | 1.630
3.3 |  | 3.3x1.3 | 3.3x1.3 | 1.3 | 6g | 3.300 | 3.120 | 2.795 | 2.665 | 2.290 | 2.210
3.3 |  | ST3.3x1.3 | ST3.3x1.3 | 1.3 | 6g | 3.300 | 3.120 | 2.795 | 2.665 | 2.290 | 2.210
3.5 |  | 3.5x1.3 | 3.5x1.3 | 1.3 | 6g | 3.530 | 3.350 | 3.085 | 2.930 | 2.640 | 2.510
3.5 |  | ST3.5x1.3 | ST3.5x1.3 | 1.3 | 6g | 3.530 | 3.350 | 3.085 | 2.930 | 2.640 | 2.510
3.5 |  | 3.5x1.6 | 3.5x1.6 | 1.6 | 6g | 3.530 | 3.350 | 2.920 | 2.755 | 2.310 | 2.160
3.5 |  | 3.5x3.2 | 3.5x3.2 | 3.2 | 6g | 3.530 | 3.310 | 2.800 | 2.600 | 2.070 | 1.890
3.9 |  | 3.9x1.3 | 3.9x1.3 | 1.3 | 6g | 3.910 | 3.730 | 3.415 | 3.250 | 2.920 | 2.770
3.9 |  | ST3.9x1.3 | ST3.9x1.3 | 1.3 | 6g | 3.910 | 3.730 | 3.415 | 3.250 | 2.920 | 2.770
3.9 |  | 3.9x1.6 | 3.9x1.6 | 1.6 | 6g | 3.910 | 3.730 | 3.300 | 3.135 | 2.690 | 2.540
3.9 |  | 3.9x3.2 | 3.9x3.2 | 3.2 | 6g | 3.910 | 3.690 | 3.180 | 2.980 | 2.450 | 2.270
4.2 |  | 4.2x1.4 | 4.2x1.4 | 1.4 | 6g | 4.220 | 4.040 | 3.660 | 3.495 | 3.100 | 2.950
4.2 |  | ST4.2x1.4 | ST4.2x1.4 | 1.4 | 6g | 4.220 | 4.040 | 3.660 | 3.495 | 3.100 | 2.950
4.2 |  | 4.2x1.6 | 4.2x1.6 | 1.6 | 6g | 4.220 | 4.040 | 3.610 | 3.445 | 3.000 | 2.850
4.2 |  | 4.2x3.2 | 4.2x3.2 | 3.2 | 6g | 4.220 | 4.000 | 3.380 | 3.180 | 2.540 | 2.360
4.8 |  | 4.8x1.6 | 4.8x1.6 | 1.6 | 6g | 4.800 | 4.620 | 4.190 | 4.025 | 3.580 | 3.430
4.8 |  | ST4.8x1.6 | ST4.8x1.6 | 1.6 | 6g | 4.800 | 4.620 | 4.190 | 4.025 | 3.580 | 3.430
4.8 |  | 4.8x1.8 | 4.8x1.8 | 1.8 | 6g | 4.800 | 4.620 | 4.065 | 3.885 | 3.330 | 3.150
4.8 |  | 4.8x3.2 | 4.8x3.2 | 3.2 | 6g | 4.800 | 4.580 | 3.960 | 3.760 | 3.120 | 2.940
5.5 |  | 5.5x1.8 | 5.5x1.8 | 1.8 | 6g | 5.460 | 5.280 | 4.815 | 4.635 | 4.170 | 3.990
5.5 |  | ST5.5x1.8 | ST5.5x1.8 | 1.8 | 6g | 5.460 | 5.280 | 4.815 | 4.635 | 4.170 | 3.990
6.3 |  | 6.3x1.8 | 6.3x1.8 | 1.8 | 6g | 6.250 | 6.030 | 5.565 | 5.365 | 4.880 | 4.700
6.3 |  | ST6.3x1.8 | ST6.3x1.8 | 1.8 | 6g | 6.250 | 6.030 | 5.565 | 5.365 | 4.880 | 4.700
8.0 |  | 8x2.1 | 8x2.1 | 2.1 | 6g | 8.000 | 7.780 | 7.100 | 6.885 | 6.200 | 5.990
8.0 |  | ST8x2.1 | ST8x2.1 | 2.1 | 6g | 8.000 | 7.780 | 7.100 | 6.885 | 6.200 | 5.990
9.5 |  | 9.5x2.1 | 9.5x2.1 | 2.1 | 6g | 9.650 | 9.430 | 8.750 | 8.510 | 7.850 | 7.590
9.5 |  | ST9.5x2.1 | ST9.5x2.1 | 2.1 | 6g | 9.650 | 9.430 | 8.750 | 8.510 | 7.850 | 7.590

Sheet: ISO Pipe Threads
M Q | ISO Pipe Threads |  | Sort Order - 9 |  | External |  |  |  |  |  |  | Internal
 |  |  |  |  |  | Major Dia |  | Pitch Dia |  | Minor Dia |  |  | Minor Dia |  | Pitch Dia |  | Major Dia |  | Tap Drill | Thread Depth | Thread Runouts
Size | Size Suffix | Thread Designation | Custom Thread Designation | TPI | Class | Max | Min | Max | Min | Max | Min | Class | Min | Max | Min | Max | Min | Max | Basic
7.723 |  | G7.723x0.907 | G 1/16 | 28 | A | 7.723 | 7.509 | 7.142 | 7.035 | 6.561 |  |  | 6.561 | 6.834 | 7.142 | 7.249 | 7.723 |  | 1.5875 | 15.446 | 4.5000
7.723 |  | G7.723x0.907 | G 1/16 | 28 | B | 7.723 | 7.509 | 7.142 | 6.928 | 6.561
9.728 |  | G9.728x0.907 | G 1/8 | 28 | A | 9.728 | 9.514 | 9.147 | 9.040 | 8.566 |  |  | 8.566 | 8.848 | 9.147 | 9.254 | 9.728 |  | 3.1750 | 19.456 | 4.5000
9.728 |  | G9.728x0.907 | G 1/8 | 28 | B | 9.728 | 9.514 | 9.147 | 8.933 | 8.566
13.157 |  | G13.157x1.337 | G 1/4 | 19 | A | 13.157 | 12.907 | 12.301 | 12.176 | 11.445 |  |  | 11.445 | 11.89 | 12.301 | 12.426 | 13.157 |  | 6.3500 | 26.314 | 6.5000
13.157 |  | G13.157x1.337 | G 1/4 | 19 | B | 13.157 | 12.907 | 12.301 | 12.051 | 11.445
16.662 |  | G16.662x1.337 | G 3/8 | 19 | A | 16.662 | 16.412 | 15.806 | 15.681 | 14.950 |  |  | 14.95 | 15.395 | 15.806 | 15.931 | 16.662 |  | 9.5250 | 33.324 | 6.5000
16.662 |  | G16.662x1.337 | G 3/8 | 19 | B | 16.662 | 16.412 | 15.806 | 15.556 | 14.950
20.955 |  | G20.955x1.814 | G 1/2 | 14 | A | 20.955 | 20.671 | 19.793 | 19.651 | 18.631 |  |  | 18.631 | 19.172 | 19.793 | 19.935 | 20.955 |  | 12.7000 | 41.910 | 8.5000
20.955 |  | G20.955x1.814 | G 1/2 | 14 | B | 20.955 | 20.671 | 19.793 | 19.509 | 18.631
22.911 |  | G22.911x1.814 | G 5/8 | 14 | A | 22.911 | 22.627 | 21.749 | 21.607 | 20.587 |  |  | 20.587 | 21.128 | 21.749 | 21.891 | 22.911 |  |  | 45.822 | 8.5000
22.911 |  | G22.911x1.814 | G 5/8 | 14 | B | 22.911 | 22.627 | 21.749 | 21.465 | 20.587
26.441 |  | G26.441x1.814 | G 3/4 | 14 | A | 26.441 | 26.157 | 25.279 | 25.137 | 24.117 |  |  | 24.117 | 24.658 | 25.279 | 25.421 | 26.441 |  | 15.8750 | 52.882 | 8.5000
26.441 |  | G26.441x1.814 | G 3/4 | 14 | B | 26.441 | 26.157 | 25.279 | 24.995 | 24.117
30.201 |  | G30.201x1.814 | G 7/8 | 14 | A | 30.201 | 29.917 | 29.039 | 28.897 | 27.877 |  |  | 27.877 | 28.418 | 29.039 | 29.181 | 30.201 |  | 22.2250 | 60.402 | 8.5000
30.201 |  | G30.201x1.814 | G 7/8 | 14 | B | 30.201 | 29.917 | 29.039 | 28.755 | 27.877
33.249 |  | G33.249x2.309 | G 1 | 11 | A | 33.249 | 32.889 | 31.770 | 31.590 | 30.291 |  |  | 30.291 | 30.931 | 31.77 | 31.95 | 33.249 |  | 25.4000 | 66.498 | 10.0000
33.249 |  | G33.249x2.309 | G 1 | 11 | B | 33.249 | 32.889 | 31.770 | 31.410 | 30.291
37.897 |  | G37.897x2.309 | G 1 1/8 | 11 | A | 37.897 | 37.537 | 36.418 | 36.238 | 34.939 |  |  | 34.939 | 35.579 | 36.418 | 36.598 | 37.897 |  | 28.5750 | 75.794 | 10.0000
37.897 |  | G37.897x2.309 | G 1 1/8 | 11 | B | 37.897 | 37.537 | 36.418 | 36.058 | 34.939
41.910 |  | G41.91x2.309 | G 1 1/4 | 11 | A | 41.910 | 41.550 | 40.431 | 40.251 | 38.952 |  |  | 38.952 | 39.592 | 40.431 | 40.611 | 41.910 |  | 31.7500 | 83.820 | 10.0000
41.910 |  | G41.91x2.309 | G 1 1/4 | 11 | B | 41.910 | 41.550 | 40.431 | 40.071 | 38.952
47.803 |  | G47.803x2.309 | G 1 1/2 | 11 | A | 47.803 | 47.443 | 46.324 | 46.144 | 44.845 |  |  | 44.845 | 45.485 | 46.324 | 46.504 | 47.803 |  | 38.1000 | 95.606 | 10.0000
47.803 |  | G47.803x2.309 | G 1 1/2 | 11 | B | 47.803 | 47.443 | 46.324 | 45.964 | 44.845
53.746 |  | G53.746x2.309 | G 1 3/4 | 11 | A | 53.746 | 53.386 | 52.267 | 52.087 | 50.788 |  |  | 50.788 | 51.428 | 52.267 | 52.447 | 53.746 |  | 44.4500 | 107.492 | 10.0000
53.746 |  | G53.746x2.309 | G 1 3/4 | 11 | B | 53.746 | 53.386 | 52.267 | 51.907 | 50.788
59.614 |  | G59.614x2.309 | G 2 | 11 | A | 59.614 | 59.254 | 58.135 | 57.955 | 56.656 |  |  | 56.656 | 57.296 | 58.135 | 58.315 | 59.614 |  | 50.8000 | 119.228 | 10.0000
59.614 |  | G59.614x2.309 | G 2 | 11 | B | 59.614 | 59.254 | 58.135 | 57.775 | 56.656
65.710 |  | G65.71x2.309 | G 2 1/4 | 11 | A | 65.710 | 65.276 | 64.231 | 64.014 | 62.752 |  |  | 62.752 | 63.392 | 64.231 | 64.448 | 65.710 |  | 57.1500 | 131.420 | 10.0000
65.710 |  | G65.71x2.309 | G 2 1/4 | 11 | B | 65.710 | 65.276 | 64.231 | 63.797 | 62.752
75.184 |  | G75.184x2.309 | G 2 1/2 | 11 | A | 75.184 | 74.750 | 73.705 | 73.488 | 72.226 |  |  | 72.226 | 72.866 | 73.705 | 73.922 | 75.184 |  |  | 150.368 | 10.0000
75.184 |  | G75.184x2.309 | G 2 1/2 | 11 | B | 75.184 | 74.750 | 73.705 | 73.271 | 72.226
81.534 |  | G81.534x2.309 | G 2 3/4 | 11 | A | 81.534 | 81.100 | 80.055 | 79.838 | 78.576 |  |  | 78.576 | 79.216 | 80.055 | 80.272 | 81.534 |  | 69.8500 | 163.068 | 10.0000
81.534 |  | G81.534x2.309 | G 2 3/4 | 11 | B | 81.534 | 81.100 | 80.055 | 79.621 | 78.576
87.884 |  | G87.884x2.309 | G 3 | 11 | A | 87.884 | 87.450 | 86.405 | 86.188 | 84.926 |  |  | 84.926 | 85.566 | 86.405 | 86.622 | 87.884 |  | 76.2000 | 175.768 | 10.0000
87.884 |  | G87.884x2.309 | G 3 | 11 | B | 87.884 | 87.450 | 86.405 | 85.971 | 84.926
100.330 |  | G100.33x2.309 | G 3 1/2 | 11 | A | 100.330 | 99.896 | 98.851 | 98.634 | 97.372 |  |  | 97.372 | 98.012 | 98.851 | 99.068 | 100.330 |  | 88.9000 | 200.660 | 10.0000
100.330 |  | G100.33x2.309 | G 3 1/2 | 11 | B | 100.330 | 99.896 | 98.851 | 98.417 | 97.372
113.030 |  | G113.03x2.309 | G 4 | 11 | A | 113.030 | 112.596 | 111.551 | 111.334 | 110.072 |  |  | 110.072 | 110.712 | 111.551 | 111.768 | 113.030 |  | 101.6000 | 226.060 | 10.0000
113.030 |  | G113.03x2.309 | G 4 | 11 | B | 113.030 | 112.596 | 111.551 | 111.117 | 110.072
125.730 |  | G125.73x2.309 | G 4 1/2 | 11 | A | 125.730 | 125.296 | 124.251 | 124.034 | 122.772 |  |  | 122.772 | 123.412 | 124.251 | 124.468 | 125.730 |  | 114.3000 | 251.460 | 10.0000
125.730 |  | G125.73x2.309 | G 4 1/2 | 11 | B | 125.730 | 125.296 | 124.251 | 123.817 | 122.772
138.430 |  | G138.43x2.309 | G 5 | 11 | A | 138.430 | 137.996 | 136.951 | 136.734 | 135.472 |  |  | 135.472 | 136.112 | 136.951 | 137.168 | 138.430 |  | 127.0000 | 276.860 | 10.0000
138.430 |  | G138.43x2.309 | G 5 | 11 | B | 138.430 | 137.996 | 136.951 | 136.517 | 135.472
151.130 |  | G151.13x2.309 | G 5 1/2 | 11 | A | 151.130 | 150.696 | 149.651 | 149.434 | 148.172 |  |  | 148.172 | 148.812 | 149.651 | 149.868 | 151.130 |  | 139.7000 | 302.260 | 10.0000
151.130 |  | G151.13x2.309 | G 5 1/2 | 11 | B | 151.130 | 150.696 | 149.651 | 149.217 | 148.172
163.830 |  | G163.83x2.309 | G 6 | 11 | A | 163.830 | 163.396 | 162.351 | 162.134 | 160.872 |  |  | 160.872 | 161.512 | 162.351 | 162.568 | 163.830 |  | 152.4000 | 327.660 | 10.0000
163.830 |  | G163.83x2.309 | G 6 | 11 | B | 163.830 | 163.396 | 162.351 | 161.917 | 160.872

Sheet: JIS Pipe Threads
M Q | JIS Pipe Threads |  | Sort Order -12 |  | External |  |  |  |  |  |  | Internal
 |  |  |  |  |  | Major Dia |  | Pitch Dia |  | Minor Dia |  |  | Minor Dia |  | Pitch Dia |  | Major Dia |  | Tap Drill | Thread Depth | Thread Runouts
Size | Size Suffix | Thread Designation | Custom Thread Designation | TPI | Class | Max | Min | Max | Min | Max | Min | Class | Min | Max | Min | Max | Min | Max | Basic |  | Basic
7.723 |  | G7.723x0.907 | G 1/16 | 28 | A | 7.723 | 7.509 | 7.142 | 7.035 | 6.561 |  |  | 6.561 | 6.834 | 7.142 | 7.249 | 7.723 |  | 1.5875 | 15.446 | 4.5000
7.723 |  | G7.723x0.907 | G 1/16 | 28 | B | 7.723 | 7.509 | 7.142 | 6.928 | 6.561
9.728 |  | G9.728x0.907 | G 1/8 | 28 | A | 9.728 | 9.514 | 9.147 | 9.040 | 8.566 |  |  | 8.566 | 8.848 | 9.147 | 9.254 | 9.728 |  | 3.1750 | 19.456 | 4.5000
9.728 |  | G9.728x0.907 | G 1/8 | 28 | B | 9.728 | 9.514 | 9.147 | 8.933 | 8.566
13.157 |  | G13.157x1.337 | G 1/4 | 19 | A | 13.157 | 12.907 | 12.301 | 12.176 | 11.445 |  |  | 11.445 | 11.89 | 12.301 | 12.426 | 13.157 |  | 6.3500 | 26.314 | 6.5000
13.157 |  | G13.157x1.337 | G 1/4 | 19 | B | 13.157 | 12.907 | 12.301 | 12.051 | 11.445
16.662 |  | G16.662x1.337 | G 3/8 | 19 | A | 16.662 | 16.412 | 15.806 | 15.681 | 14.950 |  |  | 14.95 | 15.395 | 15.806 | 15.931 | 16.662 |  | 9.5250 | 33.324 | 6.5000
16.662 |  | G16.662x1.337 | G 3/8 | 19 | B | 16.662 | 16.412 | 15.806 | 15.556 | 14.950
20.955 |  | G20.955x1.814 | G 1/2 | 14 | A | 20.955 | 20.671 | 19.793 | 19.651 | 18.631 |  |  | 18.631 | 19.172 | 19.793 | 19.935 | 20.955 |  | 12.7000 | 41.910 | 8.5000
20.955 |  | G20.955x1.814 | G 1/2 | 14 | B | 20.955 | 20.671 | 19.793 | 19.509 | 18.631
22.911 |  | G22.911x1.814 | G 5/8 | 14 | A | 22.911 | 22.627 | 21.749 | 21.607 | 20.587 |  |  | 20.587 | 21.128 | 21.749 | 21.891 | 22.911 |  |  | 45.822 | 8.5000
22.911 |  | G22.911x1.814 | G 5/8 | 14 | B | 22.911 | 22.627 | 21.749 | 21.465 | 20.587
26.441 |  | G26.441x1.814 | G 3/4 | 14 | A | 26.441 | 26.157 | 25.279 | 25.137 | 24.117 |  |  | 24.117 | 24.658 | 25.279 | 25.421 | 26.441 |  | 15.8750 | 52.882 | 8.5000
26.441 |  | G26.441x1.814 | G 3/4 | 14 | B | 26.441 | 26.157 | 25.279 | 24.995 | 24.117
30.201 |  | G30.201x1.814 | G 7/8 | 14 | A | 30.201 | 29.917 | 29.039 | 28.897 | 27.877 |  |  | 27.877 | 28.418 | 29.039 | 29.181 | 30.201 |  | 22.2250 | 60.402 | 8.8000
30.201 |  | G30.201x1.814 | G 7/8 | 14 | B | 30.201 | 29.917 | 29.039 | 28.755 | 27.877
33.249 |  | G33.249x2.309 | G 1 | 11 | A | 33.249 | 32.889 | 31.770 | 31.590 | 30.291 |  |  | 30.291 | 30.931 | 31.77 | 31.95 | 33.249 |  | 25.4000 | 66.498 | 10.0000
33.249 |  | G33.249x2.309 | G 1 | 11 | B | 33.249 | 32.889 | 31.770 | 31.410 | 30.291
37.897 |  | G37.897x2.309 | G 1 1/8 | 11 | A | 37.897 | 37.537 | 36.418 | 36.238 | 34.939 |  |  | 34.939 | 35.579 | 36.418 | 36.598 | 37.897 |  | 28.5750 | 75.794 | 10.0000
37.897 |  | G37.897x2.309 | G 1 1/8 | 11 | B | 37.897 | 37.537 | 36.418 | 36.058 | 34.939
41.910 |  | G41.91x2.309 | G 1 1/4 | 11 | A | 41.910 | 41.550 | 40.431 | 40.251 | 38.952 |  |  | 38.952 | 39.592 | 40.431 | 40.611 | 41.910 |  | 31.7500 | 83.820 | 10.0000
41.910 |  | G41.91x2.309 | G 1 1/4 | 11 | B | 41.910 | 41.550 | 40.431 | 40.071 | 38.952
47.803 |  | G47.803x2.309 | G 1 1/2 | 11 | A | 47.803 | 47.443 | 46.324 | 46.144 | 44.845 |  |  | 44.845 | 45.485 | 46.324 | 46.504 | 47.803 |  | 38.1000 | 95.606 | 10.0000
47.803 |  | G47.803x2.309 | G 1 1/2 | 11 | B | 47.803 | 47.443 | 46.324 | 45.964 | 44.845
53.746 |  | G53.746x2.309 | G 1 3/4 | 11 | A | 53.746 | 53.386 | 52.267 | 52.087 | 50.788 |  |  | 50.788 | 51.428 | 52.267 | 52.447 | 53.746 |  | 44.4500 | 107.492 | 10.0000
53.746 |  | G53.746x2.309 | G 1 3/4 | 11 | B | 53.746 | 53.386 | 52.267 | 51.907 | 50.788
59.614 |  | G59.614x2.309 | G 2 | 11 | A | 59.614 | 59.254 | 58.135 | 57.955 | 56.656 |  |  | 56.656 | 57.296 | 58.135 | 58.315 | 59.614 |  | 50.8000 | 119.228 | 10.0000
59.614 |  | G59.614x2.309 | G 2 | 11 | B | 59.614 | 59.254 | 58.135 | 57.775 | 56.656
65.710 |  | G65.71x2.309 | G 2 1/4 | 11 | A | 65.710 | 65.276 | 64.231 | 64.014 | 62.752 |  |  | 62.752 | 63.392 | 64.231 | 64.448 | 65.710 |  | 57.1500 | 131.420 | 10.0000
65.710 |  | G65.71x2.309 | G 2 1/4 | 11 | B | 65.710 | 65.276 | 64.231 | 63.797 | 62.752
75.184 |  | G75.184x2.309 | G 2 1/2 | 11 | A | 75.184 | 74.750 | 73.705 | 73.488 | 72.226 |  |  | 72.226 | 72.866 | 73.705 | 73.922 | 75.184 |  |  | 150.368 | 10.0000
75.184 |  | G75.184x2.309 | G 2 1/2 | 11 | B | 75.184 | 74.750 | 73.705 | 73.271 | 72.226
81.534 |  | G81.534x2.309 | G 2 3/4 | 11 | A | 81.534 | 81.100 | 80.055 | 79.838 | 78.576 |  |  | 78.576 | 79.216 | 80.055 | 80.272 | 81.534 |  | 69.8500 | 163.068 | 10.0000
81.534 |  | G81.534x2.309 | G 2 3/4 | 11 | B | 81.534 | 81.100 | 80.055 | 79.621 | 78.576
87.884 |  | G87.884x2.309 | G 3 | 11 | A | 87.884 | 87.450 | 86.405 | 86.188 | 84.926 |  |  | 84.926 | 85.566 | 86.405 | 86.622 | 87.884 |  | 76.2000 | 175.768 | 10.0000
87.884 |  | G87.884x2.309 | G 3 | 11 | B | 87.884 | 87.450 | 86.405 | 85.971 | 84.926
100.330 |  | G100.33x2.309 | G 3 1/2 | 11 | A | 100.330 | 99.896 | 98.851 | 98.634 | 97.372 |  |  | 97.372 | 98.012 | 98.851 | 99.068 | 100.330 |  | 88.9000 | 200.660 | 10.0000
100.330 |  | G100.33x2.309 | G 3 1/2 | 11 | B | 100.330 | 99.896 | 98.851 | 98.417 | 97.372
113.030 |  | G113.03x2.309 | G 4 | 11 | A | 113.030 | 112.596 | 111.551 | 111.334 | 110.072 |  |  | 110.072 | 110.712 | 111.551 | 111.768 | 113.030 |  | 101.6000 | 226.060 | 10.0000
113.030 |  | G113.03x2.309 | G 4 | 11 | B | 113.030 | 112.596 | 111.551 | 111.117 | 110.072
125.730 |  | G125.73x2.309 | G 4 1/2 | 11 | A | 125.730 | 125.296 | 124.251 | 124.034 | 122.772 |  |  | 122.772 | 123.412 | 124.251 | 124.468 | 125.730 |  | 114.3000 | 251.460 | 10.0000
125.730 |  | G125.73x2.309 | G 4 1/2 | 11 | B | 125.730 | 125.296 | 124.251 | 123.817 | 122.772
138.430 |  | G138.43x2.309 | G 5 | 11 | A | 138.430 | 137.996 | 136.951 | 136.734 | 135.472 |  |  | 135.472 | 136.112 | 136.951 | 137.168 | 138.430 |  | 127.0000 | 276.860 | 10.0000
138.430 |  | G138.43x2.309 | G 5 | 11 | B | 138.430 | 137.996 | 136.951 | 136.517 | 135.472
151.130 |  | G151.13x2.309 | G 5 1/2 | 11 | A | 151.130 | 150.696 | 149.651 | 149.434 | 148.172 |  |  | 148.172 | 148.812 | 149.651 | 149.868 | 151.130 |  | 139.7000 | 302.260 | 10.0000
151.130 |  | G151.13x2.309 | G 5 1/2 | 11 | B | 151.130 | 150.696 | 149.651 | 149.217 | 148.172
163.830 |  | G163.83x2.309 | G 6 | 11 | A | 163.830 | 163.396 | 162.351 | 162.134 | 160.872 |  |  | 160.872 | 161.512 | 162.351 | 162.568 | 163.830 |  | 152.4000 | 327.660 | 10.0000
163.830 |  | G163.83x2.309 | G 6 | 11 | B | 163.830 | 163.396 | 162.351 | 161.917 | 160.872

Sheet: DIN Pipe Threads
M Q | DIN Pipe Threads |  | Sort Order - 18 |  | External |  |  |  |  |  |  | Internal
 |  |  |  |  |  | Major Dia |  | Pitch Dia |  | Minor Dia |  |  | Minor Dia |  | Pitch Dia |  | Major Dia |  | Tap Drill | Thread Depth | Thread Runouts
Size | Size Suffix | Thread Designation | Custom Thread Designation | TPI | Class | Max | Min | Max | Min | Max | Min | Class | Min | Max | Min | Max | Min | Max | Basic
7.723 |  | G7.723x0.907 | G 1/16 | 28 | A | 7.723 | 7.509 | 7.142 | 7.035 | 6.561 |  |  | 6.561 | 6.834 | 7.142 | 7.249 | 7.723 |  | 1.5875 | 15.446 | 4.5000
7.723 |  | G7.723x0.907 | G 1/16 | 28 | B | 7.723 | 7.509 | 7.142 | 6.928 | 6.561
9.728 |  | G9.728x0.907 | G 1/8 | 28 | A | 9.728 | 9.514 | 9.147 | 9.040 | 8.566 |  |  | 8.566 | 8.848 | 9.147 | 9.254 | 9.728 |  | 3.1750 | 19.456 | 4.5000
9.728 |  | G9.728x0.907 | G 1/8 | 28 | B | 9.728 | 9.514 | 9.147 | 8.933 | 8.566
13.157 |  | G13.157x1.337 | G 1/4 | 19 | A | 13.157 | 12.907 | 12.301 | 12.176 | 11.445 |  |  | 11.445 | 11.89 | 12.301 | 12.426 | 13.157 |  | 6.3500 | 26.314 | 6.5000
13.157 |  | G13.157x1.337 | G 1/4 | 19 | B | 13.157 | 12.907 | 12.301 | 12.051 | 11.445
16.662 |  | G16.662x1.337 | G 3/8 | 19 | A | 16.662 | 16.412 | 15.806 | 15.681 | 14.950 |  |  | 14.95 | 15.395 | 15.806 | 15.931 | 16.662 |  | 9.5250 | 33.324 | 6.5000
16.662 |  | G16.662x1.337 | G 3/8 | 19 | B | 16.662 | 16.412 | 15.806 | 15.556 | 14.950
20.955 |  | G20.955x1.814 | G 1/2 | 14 | A | 20.955 | 20.671 | 19.793 | 19.651 | 18.631 |  |  | 18.631 | 19.172 | 19.793 | 19.935 | 20.955 |  | 12.7000 | 41.910 | 8.5000
20.955 |  | G20.955x1.814 | G 1/2 | 14 | B | 20.955 | 20.671 | 19.793 | 19.509 | 18.631
22.911 |  | G22.911x1.814 | G 5/8 | 14 | A | 22.911 | 22.627 | 21.749 | 21.607 | 20.587 |  |  | 20.587 | 21.128 | 21.749 | 21.891 | 22.911 |  |  | 45.822 | 8.5000
22.911 |  | G22.911x1.814 | G 5/8 | 14 | B | 22.911 | 22.627 | 21.749 | 21.465 | 20.587
26.441 |  | G26.441x1.814 | G 3/4 | 14 | A | 26.441 | 26.157 | 25.279 | 25.137 | 24.117 |  |  | 24.117 | 24.658 | 25.279 | 25.421 | 26.441 |  | 15.8750 | 52.882 | 8.5000
26.441 |  | G26.441x1.814 | G 3/4 | 14 | B | 26.441 | 26.157 | 25.279 | 24.995 | 24.117
30.201 |  | G30.201x1.814 | G 7/8 | 14 | A | 30.201 | 29.917 | 29.039 | 28.897 | 27.877 |  |  | 27.877 | 28.418 | 29.039 | 29.181 | 30.201 |  | 22.2250 | 60.402 | 8.5000
30.201 |  | G30.201x1.814 | G 7/8 | 14 | B | 30.201 | 29.917 | 29.039 | 28.755 | 27.877
33.249 |  | G33.249x2.309 | G 1 | 11 | A | 33.249 | 32.889 | 31.770 | 31.590 | 30.291 |  |  | 30.291 | 30.931 | 31.77 | 31.95 | 33.249 |  | 25.4000 | 66.498 | 10.5000
33.249 |  | G33.249x2.309 | G 1 | 11 | B | 33.249 | 32.889 | 31.770 | 31.410 | 30.291
37.897 |  | G37.897x2.309 | G 1 1/8 | 11 | A | 37.897 | 37.537 | 36.418 | 36.238 | 34.939 |  |  | 34.939 | 35.579 | 36.418 | 36.598 | 37.897 |  | 28.5750 | 75.794 | 10.5000
37.897 |  | G37.897x2.309 | G 1 1/8 | 11 | B | 37.897 | 37.537 | 36.418 | 36.058 | 34.939
41.910 |  | G41.91x2.309 | G 1 1/4 | 11 | A | 41.910 | 41.550 | 40.431 | 40.251 | 38.952 |  |  | 38.952 | 39.592 | 40.431 | 40.611 | 41.910 |  | 31.7500 | 83.820 | 10.5000
41.910 |  | G41.91x2.309 | G 1 1/4 | 11 | B | 41.910 | 41.550 | 40.431 | 40.071 | 38.952
47.803 |  | G47.803x2.309 | G 1 1/2 | 11 | A | 47.803 | 47.443 | 46.324 | 46.144 | 44.845 |  |  | 44.845 | 45.485 | 46.324 | 46.504 | 47.803 |  | 38.1000 | 95.606 | 10.5000
47.803 |  | G47.803x2.309 | G 1 1/2 | 11 | B | 47.803 | 47.443 | 46.324 | 45.964 | 44.845
53.746 |  | G53.746x2.309 | G 1 3/4 | 11 | A | 53.746 | 53.386 | 52.267 | 52.087 | 50.788 |  |  | 50.788 | 51.428 | 52.267 | 52.447 | 53.746 |  | 44.4500 | 107.492 | 10.5000
53.746 |  | G53.746x2.309 | G 1 3/4 | 11 | B | 53.746 | 53.386 | 52.267 | 51.907 | 50.788
59.614 |  | G59.614x2.309 | G 2 | 11 | A | 59.614 | 59.254 | 58.135 | 57.955 | 56.656 |  |  | 56.656 | 57.296 | 58.135 | 58.315 | 59.614 |  | 50.8000 | 119.228 | 10.5000
59.614 |  | G59.614x2.309 | G 2 | 11 | B | 59.614 | 59.254 | 58.135 | 57.775 | 56.656
65.710 |  | G65.71x2.309 | G 2 1/4 | 11 | A | 65.710 | 65.276 | 64.231 | 64.014 | 62.752 |  |  | 62.752 | 63.392 | 64.231 | 64.448 | 65.710 |  | 57.1500 | 131.420 | 10.5000
65.710 |  | G65.71x2.309 | G 2 1/4 | 11 | B | 65.710 | 65.276 | 64.231 | 63.797 | 62.752
75.184 |  | G75.184x2.309 | G 2 1/2 | 11 | A | 75.184 | 74.750 | 73.705 | 73.488 | 72.226 |  |  | 72.226 | 72.866 | 73.705 | 73.922 | 75.184 |  |  | 150.368 | 10.5000
75.184 |  | G75.184x2.309 | G 2 1/2 | 11 | B | 75.184 | 74.750 | 73.705 | 73.271 | 72.226
81.534 |  | G81.534x2.309 | G 2 3/4 | 11 | A | 81.534 | 81.100 | 80.055 | 79.838 | 78.576 |  |  | 78.576 | 79.216 | 80.055 | 80.272 | 81.534 |  | 69.8500 | 163.068 | 10.5000
81.534 |  | G81.534x2.309 | G 2 3/4 | 11 | B | 81.534 | 81.100 | 80.055 | 79.621 | 78.576
87.884 |  | G87.884x2.309 | G 3 | 11 | A | 87.884 | 87.450 | 86.405 | 86.188 | 84.926 |  |  | 84.926 | 85.566 | 86.405 | 86.622 | 87.884 |  | 76.2000 | 175.768 | 10.5000
87.884 |  | G87.884x2.309 | G 3 | 11 | B | 87.884 | 87.450 | 86.405 | 85.971 | 84.926
100.330 |  | G100.33x2.309 | G 3 1/2 | 11 | A | 100.330 | 99.896 | 98.851 | 98.634 | 97.372 |  |  | 97.372 | 98.012 | 98.851 | 99.068 | 100.330 |  | 88.9000 | 200.660 | 10.5000
100.330 |  | G100.33x2.309 | G 3 1/2 | 11 | B | 100.330 | 99.896 | 98.851 | 98.417 | 97.372
113.030 |  | G113.03x2.309 | G 4 | 11 | A | 113.030 | 112.596 | 111.551 | 111.334 | 110.072 |  |  | 110.072 | 110.712 | 111.551 | 111.768 | 113.030 |  | 101.6000 | 226.060 | 10.5000
113.030 |  | G113.03x2.309 | G 4 | 11 | B | 113.030 | 112.596 | 111.551 | 111.117 | 110.072
125.730 |  | G125.73x2.309 | G 4 1/2 | 11 | A | 125.730 | 125.296 | 124.251 | 124.034 | 122.772 |  |  | 122.772 | 123.412 | 124.251 | 124.468 | 125.730 |  | 114.3000 | 251.460 | 10.5000
125.730 |  | G125.73x2.309 | G 4 1/2 | 11 | B | 125.730 | 125.296 | 124.251 | 123.817 | 122.772
138.430 |  | G138.43x2.309 | G 5 | 11 | A | 138.430 | 137.996 | 136.951 | 136.734 | 135.472 |  |  | 135.472 | 136.112 | 136.951 | 137.168 | 138.430 |  | 127.0000 | 276.860 | 10.5000
138.430 |  | G138.43x2.309 | G 5 | 11 | B | 138.430 | 137.996 | 136.951 | 136.517 | 135.472
151.130 |  | G151.13x2.309 | G 5 1/2 | 11 | A | 151.130 | 150.696 | 149.651 | 149.434 | 148.172 |  |  | 148.172 | 148.812 | 149.651 | 149.868 | 151.130 |  | 139.7000 | 302.260 | 10.5000
151.130 |  | G151.13x2.309 | G 5 1/2 | 11 | B | 151.130 | 150.696 | 149.651 | 149.217 | 148.172
163.830 |  | G163.83x2.309 | G 6 | 11 | A | 163.830 | 163.396 | 162.351 | 162.134 | 160.872 |  |  | 160.872 | 161.512 | 162.351 | 162.568 | 163.830 |  | 152.4000 | 327.660 | 10.5000
163.830 |  | G163.83x2.309 | G 6 | 11 | B | 163.830 | 163.396 | 162.351 | 161.917 | 160.872

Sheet: BSP Pipe Threads
M Q | BSP Pipe Threads |  | Sort Order - 19 |  | External |  |  |  |  |  |  | Internal
 |  |  |  |  |  | Major Dia |  | Pitch Dia |  | Minor Dia |  |  | Minor Dia |  | Pitch Dia |  | Major Dia |  | Tap Drill | Thread Depth | Thread Runouts
Size | Size Suffix | Thread Designation | Custom Thread Designation | TPI | Class | Max | Min | Max | Min | Max | Min | Class | Min | Max | Min | Max | Min | Max | Basic |  | Basic
1/16 |  | G 1/16-28 | G 1/16-28 | 28 | A | 7.723 | 7.509 | 7.142 | 7.035 | 6.561 |  |  | 6.561 | 6.834 | 7.142 | 7.249 | 7.723 |  | 6.6000 | 15.4460 | 4.5000
1/16 |  | G 1/16-28 | G 1/16-28 | 28 | B | 7.723 | 7.509 | 7.142 | 7.035 | 6.561
1/8 |  | G 1/8-28 | G 1/8-28 | 28 | A | 9.728 | 9.514 | 9.147 | 9.040 | 8.566 |  |  | 8.566 | 8.848 | 9.147 | 9.254 | 9.728 |  | 8.7300 | 19.4560 | 4.5000
1/8 |  | G 1/8-28 | G 1/8-28 | 28 | B | 9.728 | 9.514 | 9.147 | 9.040 | 8.566
1/4 |  | G 1/4-19 | G 1/4-19 | 19 | A | 13.157 | 12.907 | 12.301 | 12.176 | 11.445 |  |  | 11.445 | 11.89 | 12.301 | 12.426 | 13.157 |  | 11.8000 | 26.3140 | 6.5000
1/4 |  | G 1/4-19 | G 1/4-19 | 19 | B | 13.157 | 12.907 | 12.301 | 12.176 | 11.445
3/8 |  | G 3/8-19 | G 3/8-19 | 19 | A | 16.662 | 16.412 | 15.806 | 15.681 | 14.950 |  |  | 14.95 | 15.395 | 15.806 | 15.931 | 16.662 |  | 15.2500 | 33.3240 | 6.5000
3/8 |  | G 3/8-19 | G 3/8-19 | 19 | B | 16.662 | 16.412 | 15.806 | 15.681 | 14.950
1/2 |  | G 1/2-14 | G 1/2-14 | 14 | A | 20.955 | 20.671 | 19.793 | 19.651 | 18.631 |  |  | 18.631 | 19.172 | 19.793 | 19.935 | 20.955 |  | 19.0500 | 41.9100 | 8.5000
1/2 |  | G 1/2-14 | G 1/2-14 | 14 | B | 20.955 | 20.671 | 19.793 | 19.651 | 18.631
5/8 |  | G 5/8-14 | G 5/8-14 | 14 | A | 22.911 | 22.627 | 21.749 | 21.607 | 20.587 |  |  | 20.587 | 21.128 | 21.749 | 21.891 | 22.911 |  | 21.0000 | 45.8220 | 8.5000
5/8 |  | G 5/8-14 | G 5/8-14 | 14 | B | 22.911 | 22.627 | 21.749 | 21.607 | 20.587
3/4 |  | G 3/4-14 | G 3/4-14 | 14 | A | 26.441 | 26.157 | 25.279 | 25.137 | 24.117 |  |  | 24.117 | 24.658 | 25.279 | 25.421 | 26.441 |  | 24.5000 | 52.8820 | 8.5000
3/4 |  | G 3/4-14 | G 3/4-14 | 14 | B | 26.441 | 26.157 | 25.279 | 25.137 | 24.117
7/8 |  | G 7/8-14 | G 7/8-14 | 14 | A | 30.201 | 29.917 | 29.039 | 28.897 | 27.877 |  |  | 27.877 | 28.418 | 29.039 | 29.181 | 30.201 |  | 28.2500 | 60.4020 | 8.5000
7/8 |  | G 7/8-14 | G 7/8-14 | 14 | B | 30.201 | 29.917 | 29.039 | 28.897 | 27.877
1 |  | G 1-11 | G 1-11 | 11 | A | 33.249 | 32.889 | 31.770 | 31.590 | 30.291 |  |  | 30.291 | 30.931 | 31.77 | 31.95 | 33.249 |  | 30.7500 | 66.4980 | 10.0000
1 |  | G 1-11 | G 1-11 | 11 | B | 33.249 | 32.889 | 31.770 | 31.590 | 30.291
1 1/4 |  | G 1 1/4-11 | G 1 1/4-11 | 11 | A | 41.910 | 41.550 | 40.431 | 40.251 | 38.952 |  |  | 38.952 | 39.592 | 40.431 | 40.611 | 41.910 |  | 39.5000 | 83.8200 | 10.0000
1 1/4 |  | G 1 1/4-11 | G 1 1/4-11 | 11 | B | 41.910 | 41.550 | 40.431 | 40.251 | 38.952
1 1/2 |  | G 1 1/2-11 | G 1 1/2-11 | 11 | A | 47.803 | 47.443 | 46.324 | 46.144 | 44.845 |  |  | 44.845 | 45.485 | 46.324 | 46.504 | 47.803 |  | 45.5000 | 95.6060 | 10.0000
1 1/2 |  | G 1 1/2-11 | G 1 1/2-11 | 11 | B | 47.803 | 47.443 | 46.324 | 46.144 | 44.845
1 3/4 |  | G 1 3/4-11 | G 1 3/4-11 | 11 | A | 53.746 | 53.386 | 52.267 | 52.087 | 50.788 |  |  | 50.788 | 51.428 | 52.267 | 52.447 | 53.746 |  | 51.0000 | 107.4920 | 10.0000
1 3/4 |  | G 1 3/4-11 | G 1 3/4-11 | 11 | B | 53.746 | 53.386 | 52.267 | 52.087 | 50.788
2 |  | G 2-11 | G 2-11 | 11 | A | 59.614 | 59.254 | 58.135 | 57.955 | 56.656 |  |  | 56.656 | 57.296 | 58.135 | 58.315 | 59.614 |  | 57.0000 | 119.2280 | 10.0000
2 |  | G 2-11 | G 2-11 | 11 | B | 59.614 | 59.254 | 58.135 | 57.955 | 56.656
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

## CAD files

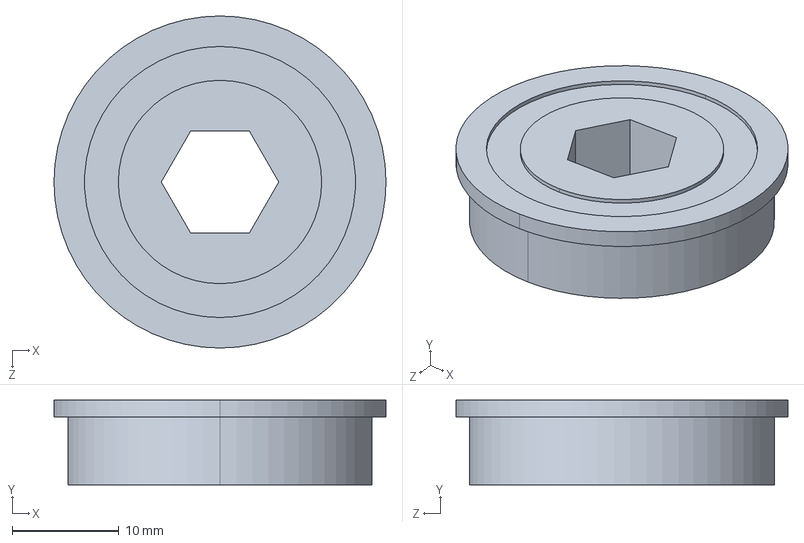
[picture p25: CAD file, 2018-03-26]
CADS/Alternate Wheel/0_375_Hex_ID_x_1_125_OD_x_0_313_WD_Flanged_Bearing_217-2735.STEP
31.1 x 7.94 x 31.1 mm

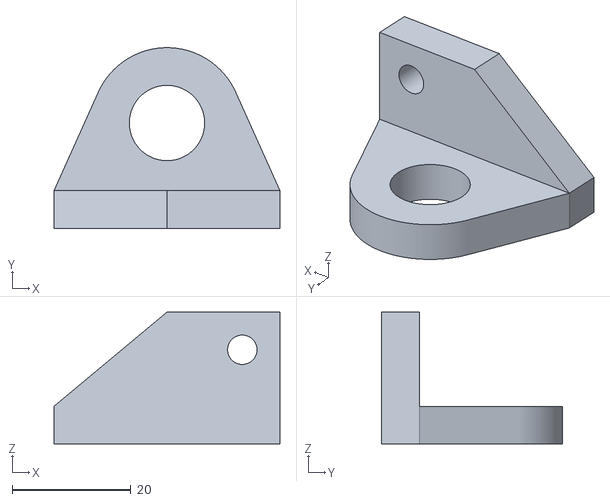
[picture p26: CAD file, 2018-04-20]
CADS/Alternate Wheel/STLs/Encoder mount_left.stl
38.1 x 30.5 x 22.2

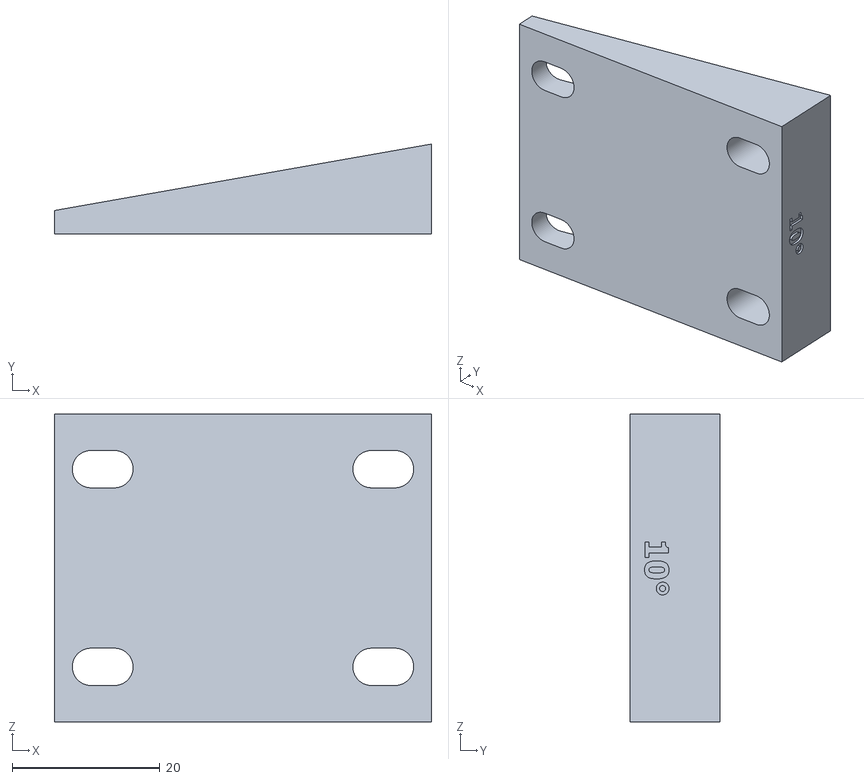
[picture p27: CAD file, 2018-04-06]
CADS/Caster Wheel mount/shim 10 Deg.stl
51.1 x 12.2 x 41.7

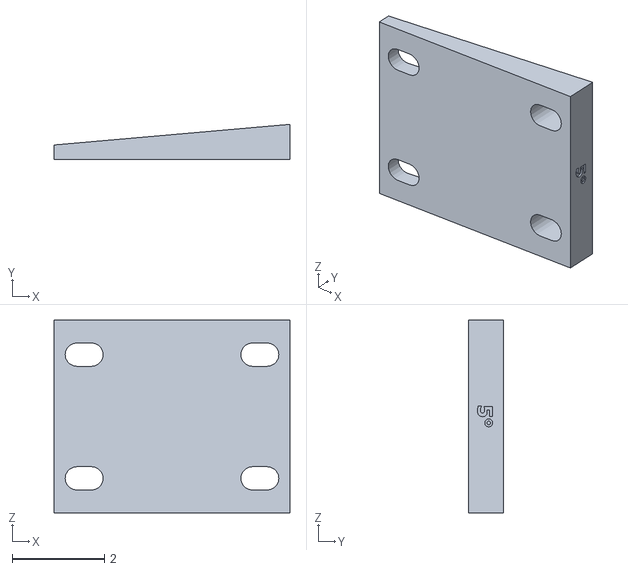
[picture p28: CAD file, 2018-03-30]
CADS/Caster Wheel mount/STLs/shim 5 Deg.stl
5.11 x 0.764 x 4.17

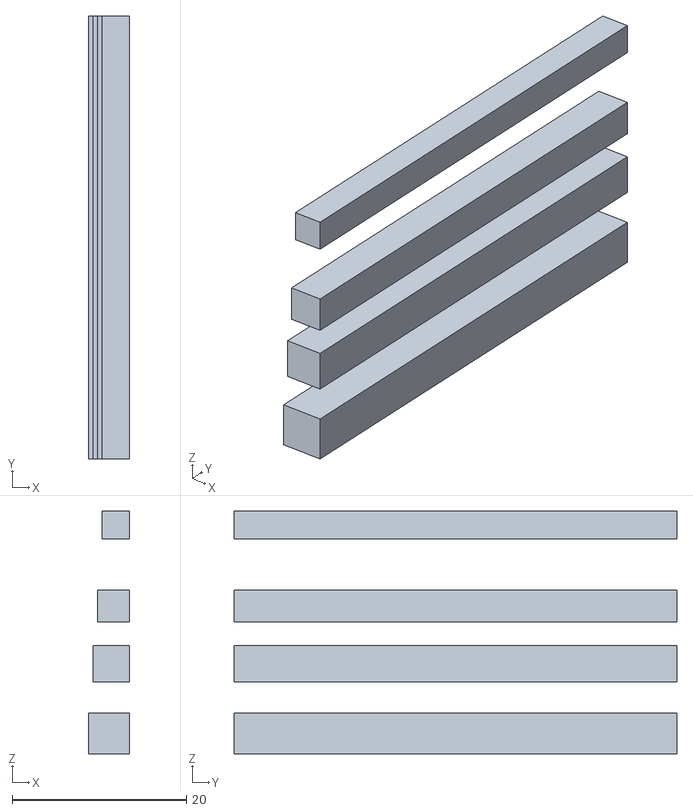
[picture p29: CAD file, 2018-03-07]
CADS/Clutch Wheel compact/STLs/Part2.stl
4.70 x 50.8 x 27.8

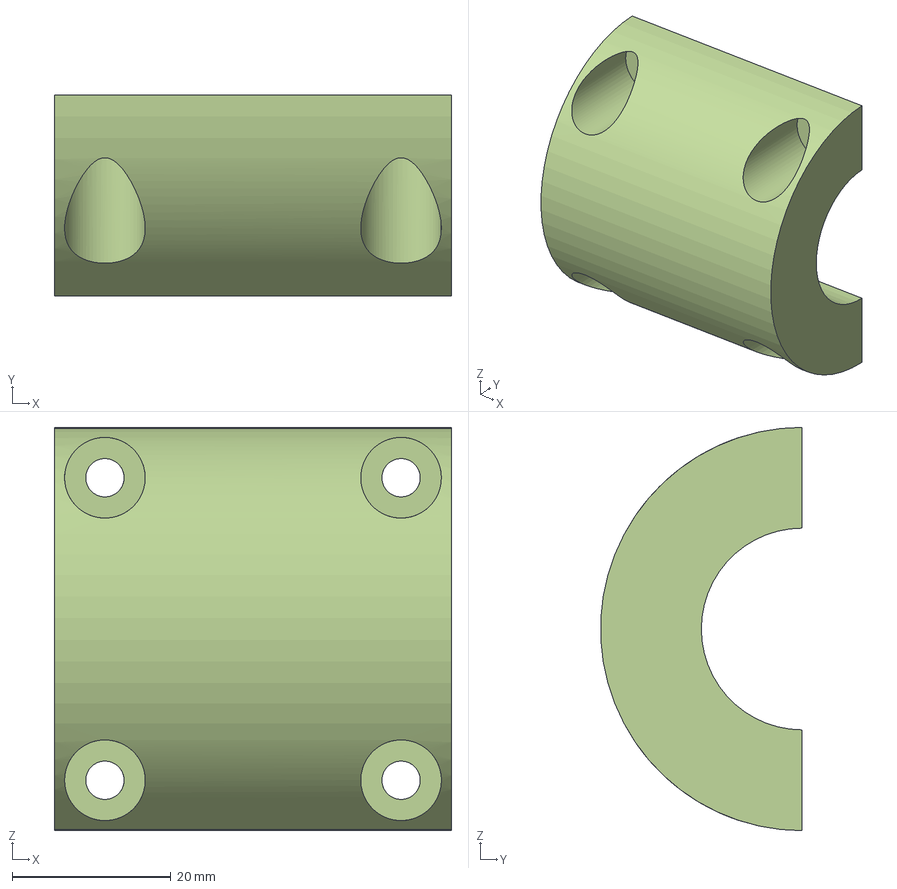
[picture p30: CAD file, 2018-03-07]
CADS/Handle CADs/Slider Mount_B.step
50.0 x 25.4 x 50.8 mm

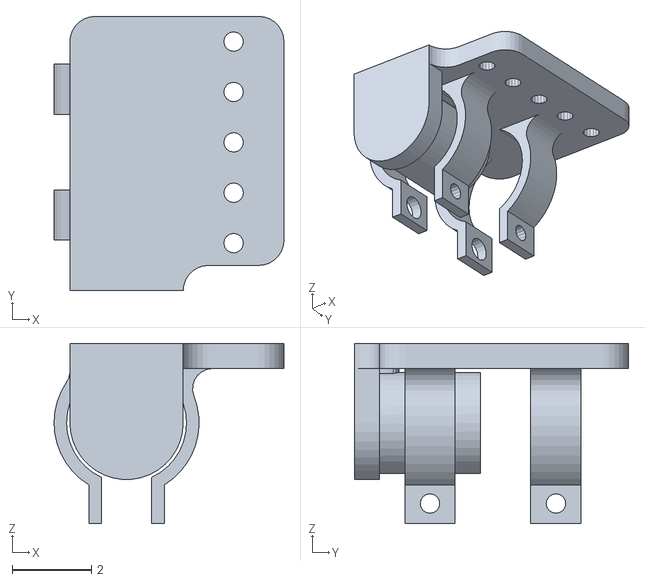
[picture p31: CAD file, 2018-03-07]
CADS/Motor Mounts/right_motor_mount.stl
5.80 x 6.91 x 4.55

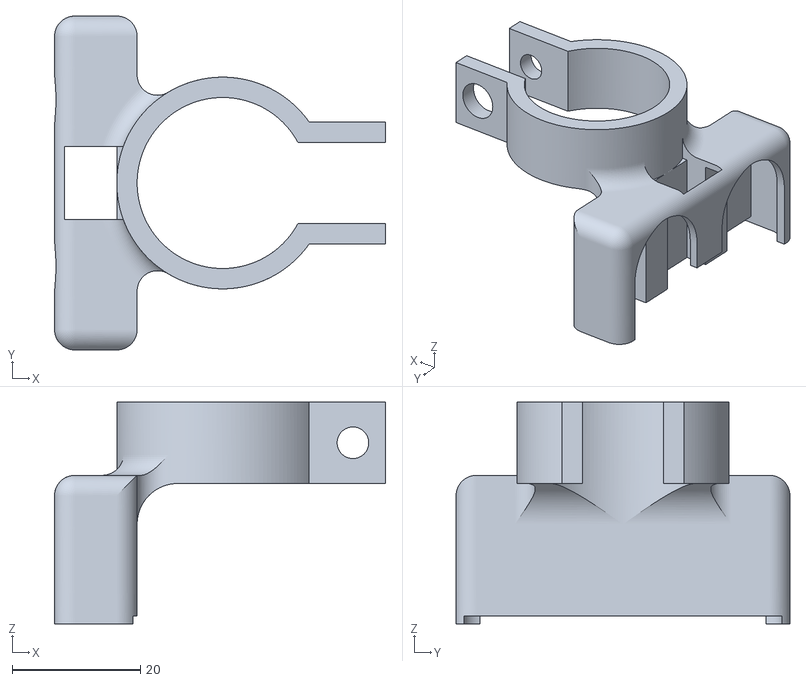
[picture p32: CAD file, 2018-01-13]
CADS/Sensor Mounts/Ultrasonic Mount 1in.stl
51.6 x 52.1 x 34.6

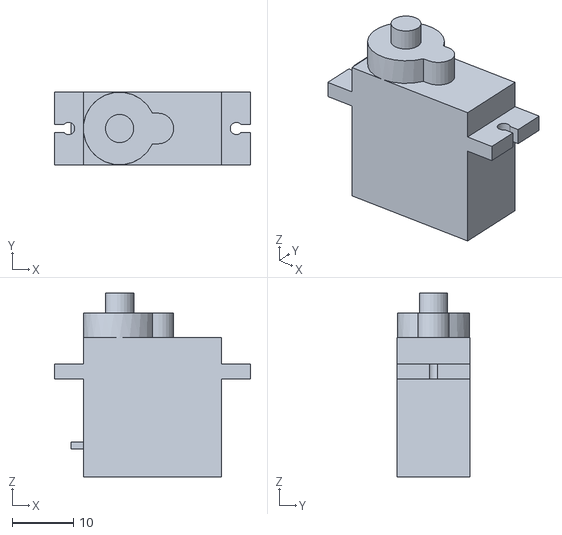
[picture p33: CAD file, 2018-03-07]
CADS/Alternate Wheel/microServo-sg90.stl
31.9 x 11.8 x 29.9

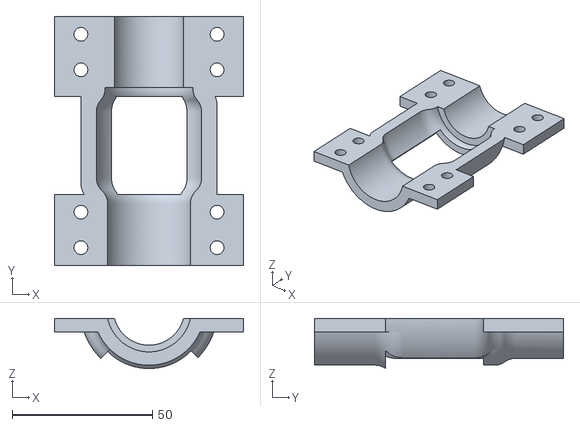
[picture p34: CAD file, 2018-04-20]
CADS/Alternate Wheel/STLs/aluminum lock.stl
67.7 x 88.9 x 17.9

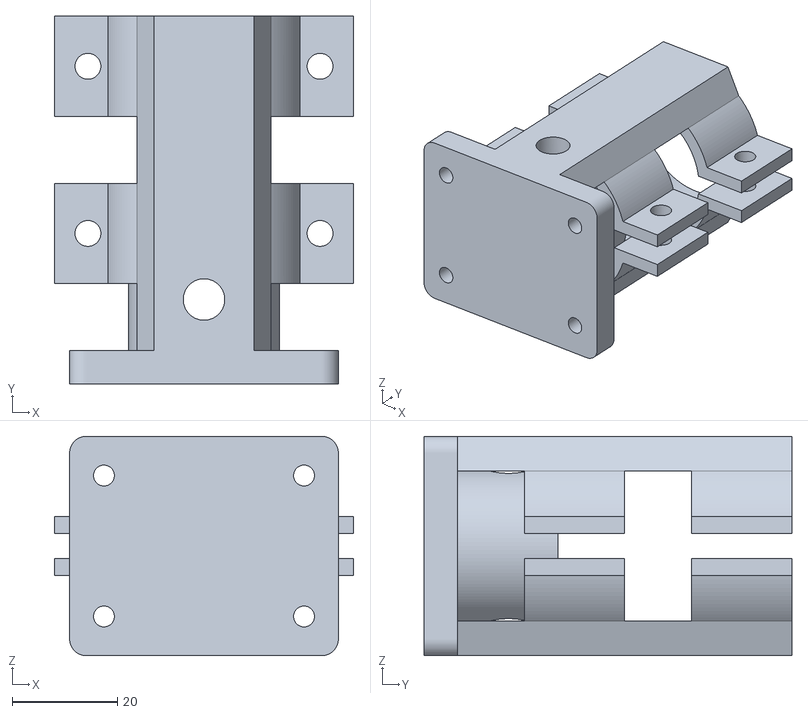
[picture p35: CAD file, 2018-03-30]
CADS/Caster Wheel mount/Mount.stl
56.8 x 69.8 x 41.7

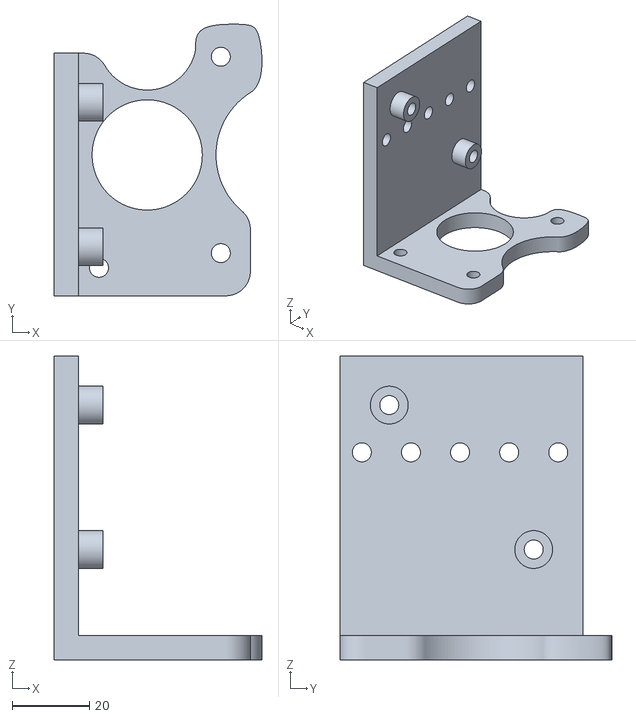
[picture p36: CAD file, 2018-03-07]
CADS/Clutch Wheel compact/STLs/motor mount 2.stl
53.8 x 70.3 x 78.6

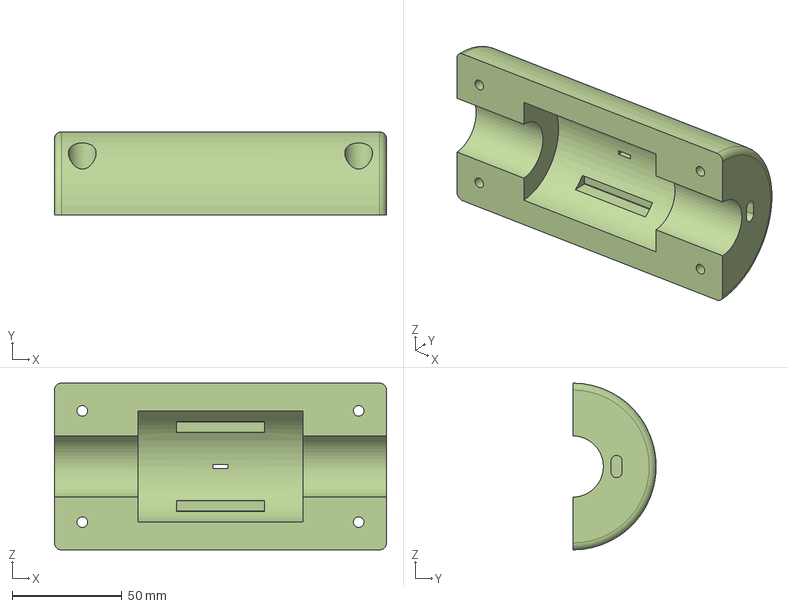
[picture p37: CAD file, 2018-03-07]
CADS/Handle CADs/Slider Mount_C.step
151.6 x 38.1 x 76.2 mm

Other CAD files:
CADS/Clutch Wheel compact/Templates/English/am_ansi.dwg
CADS/Clutch Wheel compact/Templates/Metric/am_din.dwg
CADS/Clutch Wheel compact/Templates/Standard.dwg
CADS/Clutch Wheel compact/Templates/English/ANSI (in).dwg
CADS/Clutch Wheel compact/Templates/Metric/am_bsi.dwg
CADS/Alternate Wheel/0_375_Hex_ID_x_1_125_OD_x_0_313_WD_Flanged_Bearing_217-2735.ipt
CADS/Alternate Wheel/Assembly1.iam
CADS/Alternate Wheel/Assembly2.iam
CADS/Alternate Wheel/Assembly2.ipn
CADS/Alternate Wheel/Dex shaft.ipt
CADS/Alternate Wheel/Encoder mount.ipt
CADS/Alternate Wheel/Encoder mount_left.ipt
CADS/Alternate Wheel/Encoder mount_right.ipt
CADS/Alternate Wheel/Imported Components/microServo-sg90/microServo-sg90.ipt
CADS/Alternate Wheel/OldVersions/0_375_Hex_ID_x_1_125_OD_x_0_313_WD_Flanged_Bearing_217-2735.0001.ipt
CADS/Alternate Wheel/OldVersions/Assembly1.0002.iam
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

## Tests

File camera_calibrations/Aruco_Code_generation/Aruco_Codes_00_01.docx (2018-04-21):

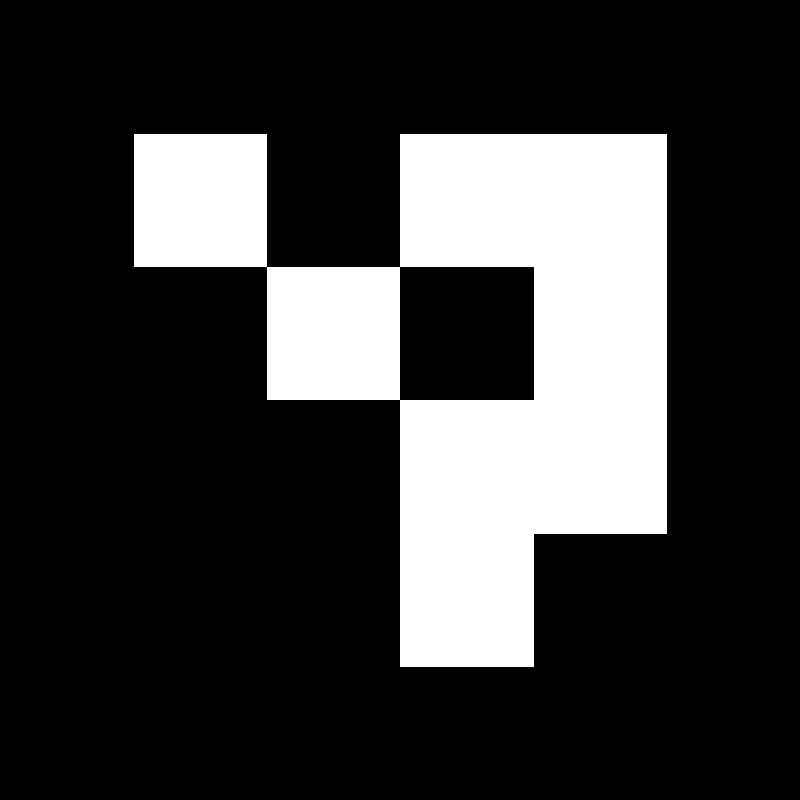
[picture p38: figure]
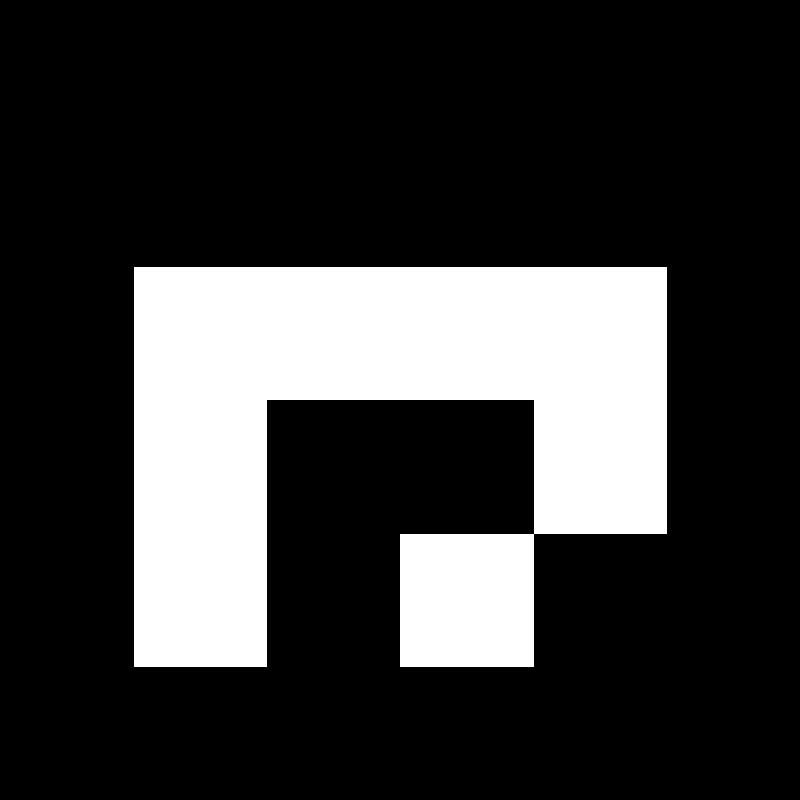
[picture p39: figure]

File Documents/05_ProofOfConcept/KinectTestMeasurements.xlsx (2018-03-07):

Sample | Expected Distance (m) | Measured Distance (m) | Angle (max or centerline) | Absolute Error | % Error
1 | 0.5000 | 0.4902 | Centerline | 0.0098 | 1.96%
2 | 0.7500 | 0.7480 | Centerline | 0.0020 | 0.27%
3 | 1.0000 | 0.9880 | Centerline | 0.0120 | 1.20%
4 | 1.2500 | 1.2400 | Centerline | 0.0100 | 0.80%
5 | 1.9200 | 1.9150 | Centerline | 0.0050 | 0.26%
6 | 2.1300 | 2.1140 | Centerline | 0.0160 | 0.75%
7 | 0.5400 | 0.5681 | Max | 0.0281 | 5.21%
8 | 0.8400 | 0.8576 | Max | 0.0176 | 2.09%
9 | 1.1100 | 1.1342 | Max | 0.0242 | 2.18%
10 | 1.4000 | 1.4104 | Max | 0.0104 | 0.75%

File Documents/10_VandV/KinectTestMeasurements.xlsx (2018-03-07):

Sample | Absolute Distance (m) | Kinect Distance (m) | Angle (max or centerline) | X | Y
1 | 0.5 | 0.4902 | Centerline
2 | 0.75 | 0.7480004278 | Centerline | 0.748 | 0.0008
3 | 1 | 0.9880247973 | Centerline | 0.988 | 0.007
4 | 1.25 | 1.240032661 | Centerline | 1.24 | 0.009
5 | 1.92 | 1.915006527 | Centerline | 1.915 | 0.005
6 | 2.13 | 2.114007417 | Centerline | 2.114 | 0.0056
7 | 0.54 | 0.5681384426 | Max | 0.4977 | 0.274
8 | 0.84 | 0.8575529138 | Max | 0.751 | 0.414
9 | 1.11 | 1.134235566 | Max | 0.9934 | 0.5474
10 | 1.4 | 1.410432054 | Max | 1.2353 | 0.6807

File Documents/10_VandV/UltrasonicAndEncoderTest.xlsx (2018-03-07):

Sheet: Sheet1
Sample | Expected Distance (m) | Measured Distance (m) | Absolute Error | % Error
1 | 0.0500 | 0.0500 | 7.450999956e-10 | 1.490199986e-06%
2 | 0.1000 | 0.0900 | 0.0100 | 10.00%
3 | 0.2000 | 0.1800 | 0.0200 | 10.00%
4 | 0.3000 | 0.2700 | 0.0300 | 10.00%
5 | 0.4000 | 0.3600 | 0.0400 | 10.00%
6 | 0.5000 | 0.4500 | 0.0500 | 10.00%
7 | 0.6000 | 0.5400 | 0.0600 | 10.00%
8 | 0.7000 | 0.6270 | 0.0730 | 10.44%
9 | 0.8000 | 0.7200 | 0.0800 | 10.00%
10 | 0.9000 | 0.8200 | 0.0800 | 8.89%
11 | 1.0000 | 0.9000 | 0.1000 | 10.00%
12 | 1.1000 | 0.9900 | 0.1100 | 10.00%
13 | 1.2000 | 1.0800 | 0.1200 | 10.00%
14 | 1.3000 | 1.1700 | 0.1300 | 10.00%
15 | 1.4000 | 1.2700 | 0.1300 | 9.29%
16 | 1.5000 | 1.3600 | 0.1400 | 9.33%
17 | 1.6000 | 1.4500 | 0.1500 | 9.37%
18 | 1.7000 | 1.5400 | 0.1600 | 9.41%
19 | 1.8000 | 1.6300 | 0.1700 | 9.44%
20 | 1.9000 | 1.7200 | 0.1800 | 9.47%
21 | 2.0000 | 1.8100 | 0.1900 | 9.50%

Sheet: Sheet2
Sample | Expected Value | Recorded Value
1 | 512 | 518
2 | 512 | 515
3 | 512 | 512
4 | 512 | 508

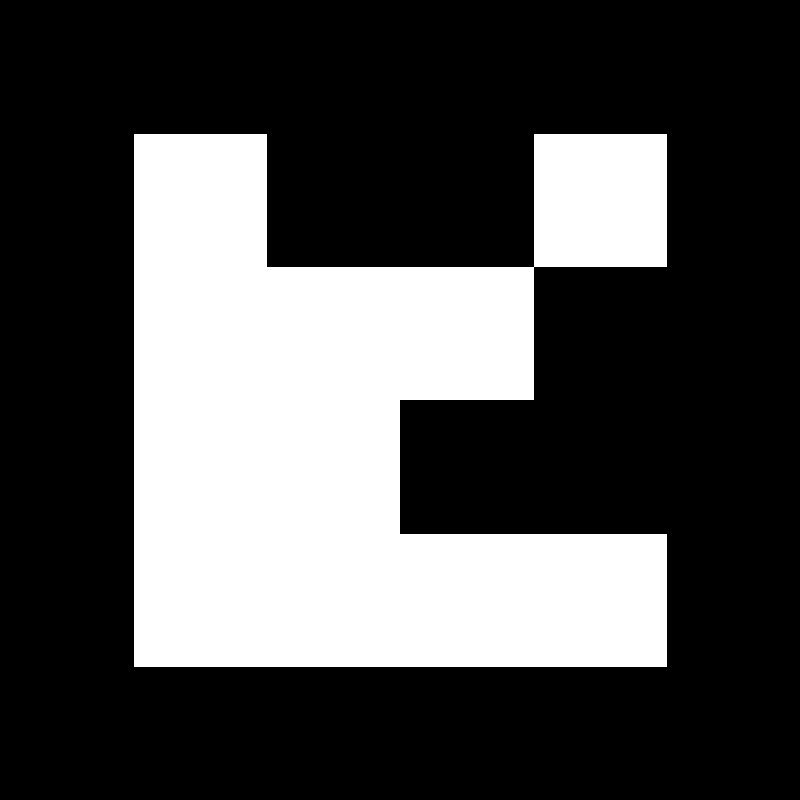
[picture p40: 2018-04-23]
camera_calibrations/Aruco_Code_generation/Markers_100/Marker_32.png

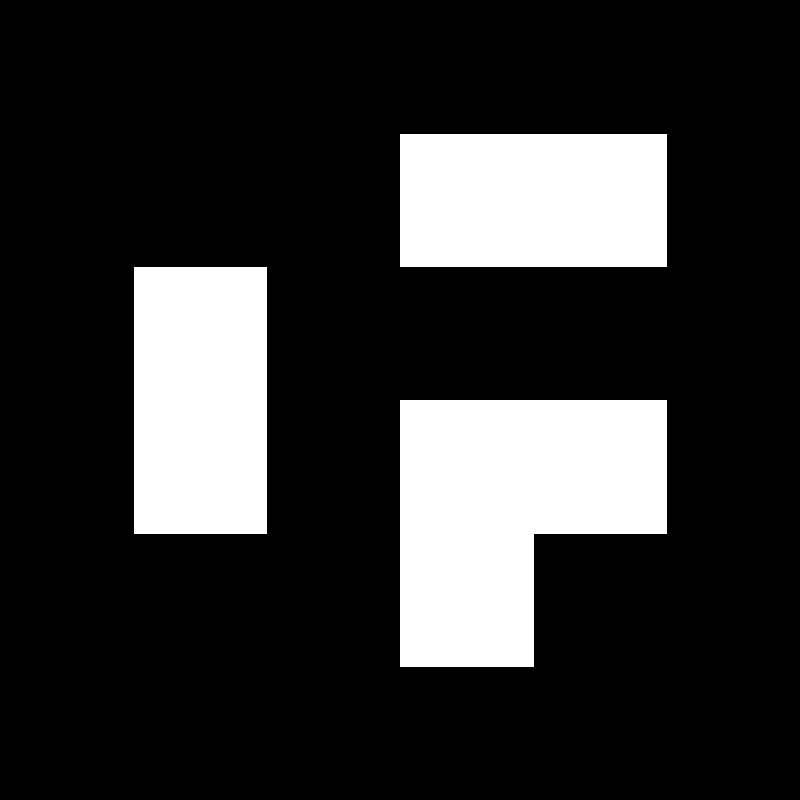
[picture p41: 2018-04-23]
camera_calibrations/Aruco_Code_generation/Markers_100/Marker_43.png

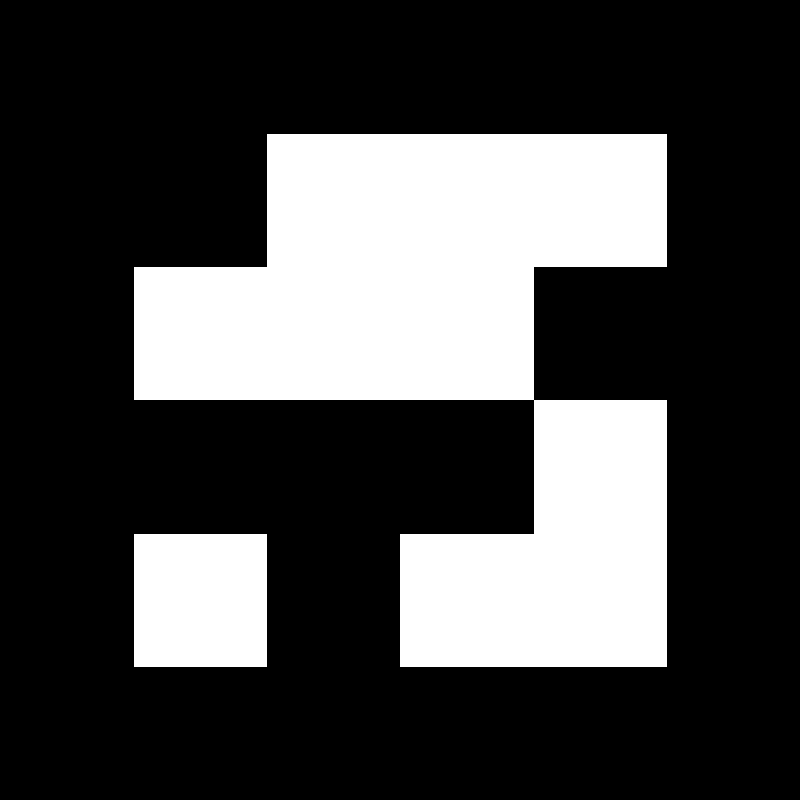
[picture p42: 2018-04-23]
camera_calibrations/Aruco_Code_generation/Markers_100/Marker_61.png

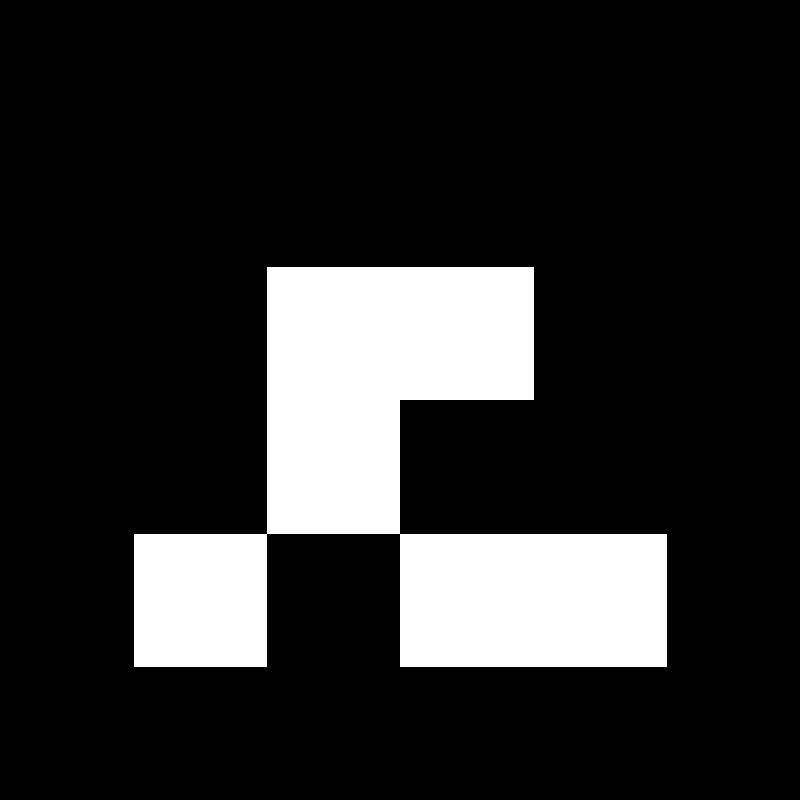
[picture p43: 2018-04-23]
camera_calibrations/Aruco_Code_generation/Markers_100/Marker_92.png

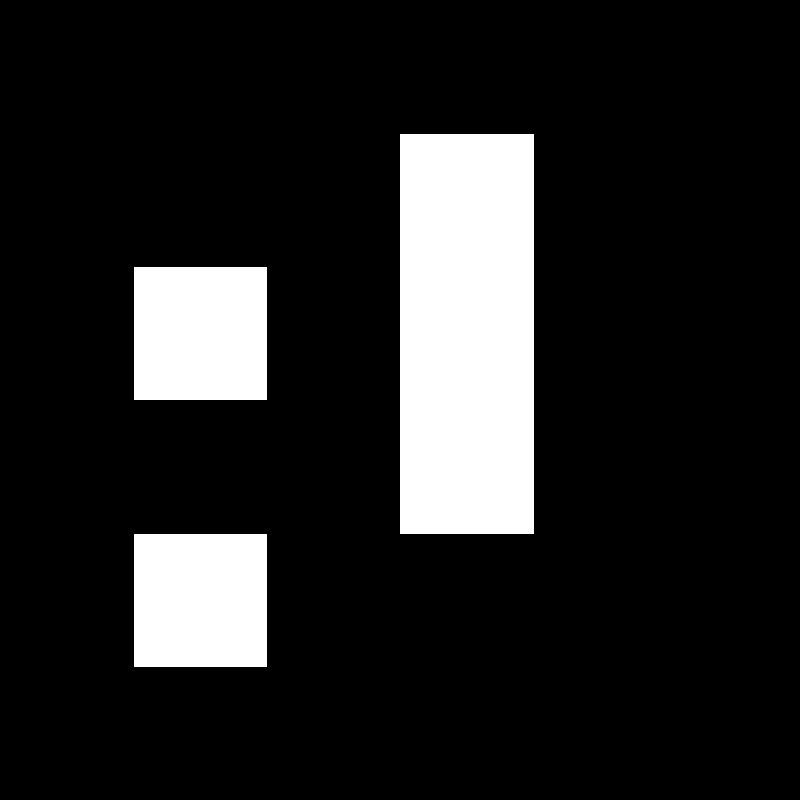
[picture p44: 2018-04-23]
camera_calibrations/Aruco_Code_generation/Markers_100/Marker_41.png

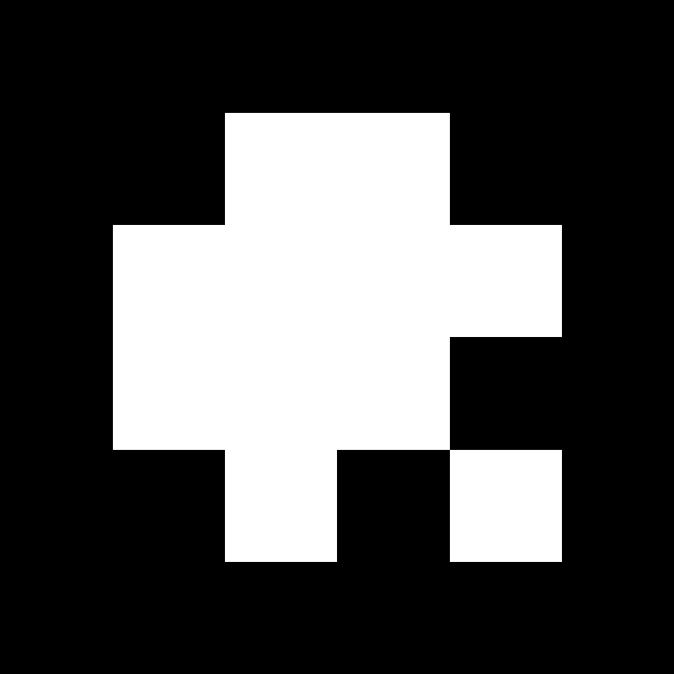
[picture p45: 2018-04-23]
camera_calibrations/Aruco_Code_generation/Markers_100/Marker_59.png

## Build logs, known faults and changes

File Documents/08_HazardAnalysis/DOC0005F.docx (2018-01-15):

# HAZARD ANALYSIS DOCUMENT

MECHATRONICS 4TB6

GROUP 2

NATHAN FUJIMOTO | 1224348
PRAKHAR GARG | 1204351
JOSH GILMOUR | 1402325
AARON JASS | 1218859
TYLER JASS | 1218857
FAUZIA KHANUM | 1209252
JACK LIU | 1215056
GAGAN SINGH | 1306242

# Table of Contents

# Table of Figures

# Table of Tables

# Revision History

Rev | Author(s) | Description of Change | Peer Reviewed | Date
- | T.Jass | Original Document | A.Jass N.Fujimoto | 04-Jan-2018
A | N.Fujimoto | Listing components | F. Khanum | 04-Jan-2018
B | J.Gilmor F.Khanum A.Jass T.Jass | Began STPA Hazard Analysis Began List of Safety Consideration Adding Component descriptions | A.Jass T.Jass | 05-Jan-2018
C | A.Jass T.Jass J.Liu | Developing component overview and component descriptions Added Introduction | N.Fujimoto J.Gilmour | 06-Jan-2018
D | N.Fujimoto J.Gilmor | Added STPA diagrams Added STPA Hazards, Hazard Table | F. Khanum | 08-Jan-2018
E | N.Fujimoto J.Gilmor F. Khanum | Completed initial draft of STPA Hazard Analysis Safety Considerations | T.Jass | 09-Jan-2018
F | T.Jass N.Fujimoto | Added System variable tables and formatted document | A.Jass | 11-Jan-2018

# 1 Introduction

The purpose of this document is to outline the components, safety considerations, and hazards for the SmartWalker. The first part of this document will provide an overview of all the various hardware and software components, along with a brief description of each component. The second part will list the safety considerations for each component as well as detail how these safety considerations will be implemented. Finally, a comprehensive analysis will be conducted of potential hazards through a Systems-Theoretic Process Analysis (STPA) approach for each of our controlled processes. In this diagram, a list of potential hazards will be compiled by analyzing the potential interaction failures in the components, and in the environment, and steps to mitigate these failures will be discussed.

# 2 Overview

## 2.1 Component Overview

The following diagram gives a high-level overview of the SmartWalker system from the inputs into the different modules to outputs per module. As seen below the system is made of four modules: the navigation module, the human interface module, the walker interface module, and the drive module. These modules will aid in finding and describing the different hazards present in the system.

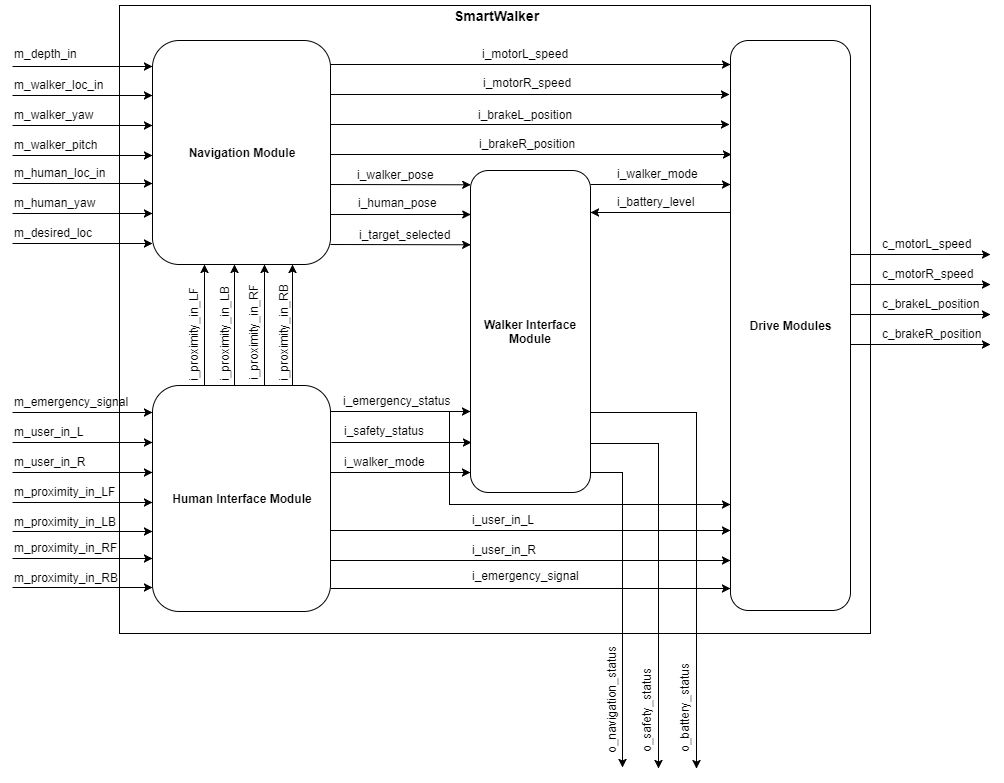
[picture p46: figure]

Figure 1 - High Level Module Diagram

## 2.2 Component Description

A description of each component (or module) is given below.

### 2.2.1 Navigation Module

This module is the main navigation module which autonomously moves the SmartWalker between two locations within a room. This module directly takes in the main navigation depth image sensor data, mapping data and user target data, while receiving information from the human interface module about manual assistive needs and proximity to other objects. It passes motor and brake commands to the drive module and passes navigation variables to the walker interface module.

### 2.2.2 Human Interface Module

This module contains the human-machine interfaces that directly get inputs from the user while in manual use like handle information and the need for emergency braking. In addition, it is connected to proximity data which collects information on approaching objects to the human (and SmartWalker). The proximity information is passed on to the Navigation Module, safety data and emergency inputs are passed on to the Walker Interface Module, and finally the user handle inputs and emergency signal are connected to the Drive Module.

### 2.2.3 Walker Interface Module

The Walker Interface Module displays information of the walker’s statuses to user while all modes. It takes in navigation information to output a navigation status to the user, as well as takes emergency status and safety status information to be displayed to the user’s mobile device and walker screen depending on the mode of operation of the SmartWalker.

### 2.2.4 Drive Modules

This module takes in the motor/brake commands outputted by the Master Control Module and executes them by actuating the motors/brakes. It also receives the desired user speed (or braking request) and emergency request and executes them in real-time by again actuating the motors/brakes.

## 2.3 System Variables

The following are several tables specifying the system’s different variables, a legend is included below providing the meaning of the prefixes:

Table 1 - System Variable Prefixes

Prefix | Meaning | Description
m | Monitored | Variables that store information from sensors about the physical environment.
c | Controlled | Variables that store information to be outputted to actuators.
i | Input | Purely software variable that is an input to a software module.
o | Output | Variable that is an output determined by a software module.

Table 2 - Monitored Variables

Variable | Description | Units | Range
m_battery_lvl | Power level of battery. | Battery Sustain of Charge (%) | [0, 100]
m_battery_rel | Reliability of the battery. | Battery Health (%) | [0, 100]
m_proximity_in_LF | Proximity to any objects in the environment (front-left side). | Distance (cm) | [0, 500]
m_proximity_in_RF | Proximity to objects in the environment (front-right side). | Distance (cm) | [0, 500]
m_proximity_in_LB | Proximity to any objects in the environment (back-left side). | Distance (cm) | [0, 500]
m_proximity_in_RB | Proximity to objects in the environment (back-right side). | Distance (cm) | [0, 500]
m_depth_in | Depth of the upcoming ground with respect to the bottom of the walker. | Distance (cm) | [-100, 0]
m_walker_yaw | Orientation of the walker (yaw) with respect to the walker’s z-axis. | Angle (deg) | [-180, 180]
m_walker_pitch | Orientation of the walker (pitch) with respect to the walker’s y-axis. | Angle (deg) | [-45, 45]
m_walker_loc_out | Global location of the walker. | [Longitude (deg), Latitude (deg)] | [-180, 180; -90,90]
m_walker_loc_in | Location of the walker inside the patient room, with respect to a preset coordinate system. | [x,y] on room map | [0, 100; 0, 100]
m_human_loc_in | Location of the human based on their phone, with respect to a preset coordinate system. | [x, y] on room map | [0, 100; 0, 100]
m_human_yaw | Orientation of the human (yaw) with respect to the human’s z-axis. | Angle (deg) | [-45, 45]
m_desired_loc | User selected desired location for the walker in autonomous mode | Enum (states) | GoDocking, GoHuman
m_dock_aligned | Walker is physically aligned with the docking station | Boolean | 0, 1
m_user_in_L | Desired forward assisted movement for the user, for the left motor. | Custom | [-100,100]
m_user_in_R | Desired forward assisted movement for the user, for the left motor. | Custom | [-100,100]
m_emergency_signal | Signal for monitoring an emergency situation. | Boolean | 0, 1

Table 3 - Controlled Variables

Variable | Description | Units | Range
c_motorL_speed | Left motor speed. | Angular velocity ( deg/s) | [0, 50]
c_motorR_speed | Right motor speed. | Angular velocity (deg/s) | [0, 50]
c_brakeL_position | Left brake position. | Brake Position (%) | [0, 100]
c_brakeR_position | Right brake position. | Brake Position (%) | [0, 100]
c_charge_walker | Charge the walker. | Boolean | 0, 1
c_dock_connected | Walker physically connected to the docking station. | Boolean | 0, 1

Table 4 - Input Variables

Variable | Description | Data Type | Range
i_motorL_speed | Left wheel motor forward speed command. | 32 bit float | [0, 2]
i_motorR_speed | Right wheel motor forward speed command. | 32 bit float | [0, 2]
i_brakeL_position | Left brake motor position command. | 32 bit float | [0, 1]
i_brakeR_position | Right brake motor position command. | 32 bit float | [0, 1]
i_walker_pose | Walker’s position and orientation within room map. | 32 bit float array (x, y, z, θ) | [0, 100; 0, 100; 0, 100; -180, 180]
i_human_pose | User’s position and orientation within room map. | 32 bit float array (x, y, z, θ) | [0, 100; 0, 100; 0, 100; -180, 180]
i_target_selected | User’s desired navigation target for walker. | Enum | USER, DOCK
i_proximity_in_LF | Proximity to objects (left-front side). | 32 bit float | [0, 500]
i_proximity_in_LB | Proximity to objects (left-back side). | 32 bit float | [0, 500]
i_proximity_in_RB | Proximity to objects (right-front side). | 32 bit float | [0, 500]
i_proximity_in_RF | Proximity to objects (right-front side). | 32 bit float | [0, 500]
i_emergency_status | Walker’s status of immediate emergencies. | Enum | NON_EMER, EMER
i_safety_status | Walker’s status of unsafe scenarios approaching. | Enum | SAFE, UNSAFE
i_walker_mode | The mode of operation. | Enum | INIT, MAN, AUTO
i_user_input_R | Requested forward assisted movement for the user, for the left motor. | 16 bit uint | [0, 1024]
i_user_input_L | Requested forward assisted movement for the user, for the right motor. | 16 bit uint | 0, 1024]
i_emergency_signal | Signal indicating an emergency situation. | Boolean | 0, 1

Table 5 - Output Variables

Variable | Description | Data Type | Range
o_navigation_status | Current state of the Walker’s navigation process | Enum | IDLE, INIT, TRAN, FINE
o_safety_status | Current state of the overall system’s safety | Enum | UNSAFE, SAFE

# 3 STPA

In order to properly identify a comprehensive list of hazards for the SmartWalker project, a STPA Hazard Analysis was completed of the main controlled processes of the walker. For each of the main controlled processes, a NRC diagram was created for each to outline the appropriate control actions. Next general hazards were outlined for each and then finally hazards were organized by the four STPA categories.

## 3.1 STPA - Navigation

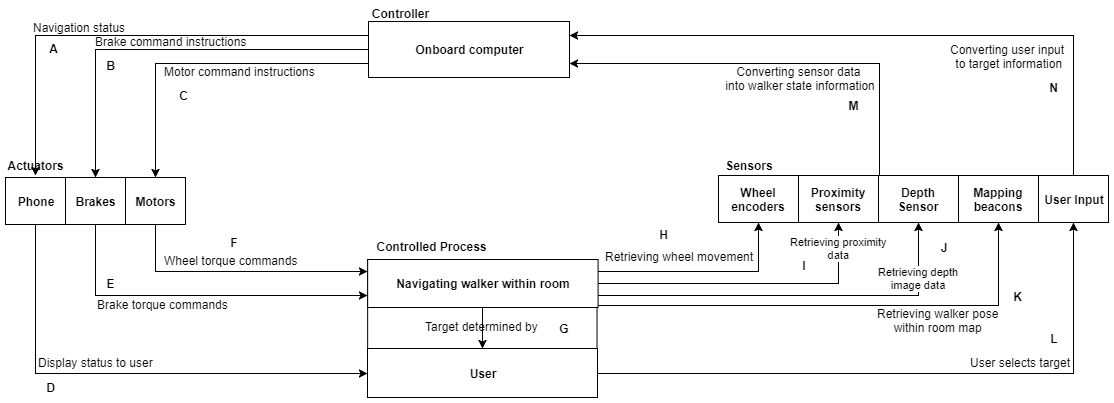
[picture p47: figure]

Figure 2 - STPA for Navigation Diagram

### 3.1.1 Control Action Hazards

Navigation Status Hazards (A):

- Incorrect status sent
- Incorrect status signal timing

Brake Command Instructions Hazards (B):

- Incorrect command sent
- Incorrect command instruction timing

Motor Command Instructions Hazards (C):

- Incorrect command sent
- Incorrect command instruction timing

Display Status to User Hazards (D):

- Operational delays
- Same as A

Brake Torque Commands Hazards (E):

- Operational delays
- Same as B

Wheel Torque Commands Hazards (F):

- Operational delays
- Same as F

Target Received Hazards (G)

- Invalid user target selection received
- Valid but incorrect user target selection received
- Incorrect user target selection timing

Retrieving Wheel Movement Hazards (H):

- Invalid wheel movement data received
- Valid but incorrect wheel movement data received
- Incorrect wheel movement data retrieval timing

Retrieving Proximity Data Hazards (I):

- Invalid proximity data received
- Valid but incorrect proximity data received
- Incorrect proximity data retrieval timing

Retrieving Depth Image Data Hazards (J):

- Invalid depth image data received
- Valid but incorrect depth image data received
- Incorrect depth image data retrieval timing

Retrieving Walker Pose within Room Map (K):

- Invalid walker pose within room map received
- Valid but incorrect walker pose within room map received
- Incorrect walker pose within room map retrieval timing

User Selects Target (L):

- Same as G

Converting Sensor Data into Walker State Information (M):

- Operational Delays
- Same as G, H, I, J, L

Converting User Input to Target Information Hazards (N):

- Operational Delays
- Same as G

### 3.1.2 STPA Hazard Analysis

Table 6 - STPA Hazard Analysis (Navigation)

Control Action | Category 1 (A control action required for safety is not provided or not followed) | Category 2 (An unsafe control action is provided that leads to a hazard) | Category 3 (A potentially safe control action is provided too early, too late, or out of sequence) | Category 4 (A safe control action is stopped too soon)
Sending Navigation Status (A, D) | System does not send navigation status when needed for the user (A1). | System sends that the walker has arrived when walker has yet to arrive (and vice-versa) (A2). | System sends walker has arrived too early or too late to the user (A3). | N/A.
Sending Brake Command Instructions (B, E) | Brake commands are not sent when requested or with an incorrect message format (B1). | System sends an inappropriate brake command for current navigation needs (B2). | Brake command is sent too early or too late which forces navigation position out of sync (B3). | Brake command is stopped too early before walker can be fully actuated (B4).
Sending Motor Command Instructions (C) | Motor commands are not sent when requested or with an incorrect message format (C1). | System sends an inappropriate motor command for current navigation needs (C2). | Motor command is sent too early or too late which forces navigation position out of sync (C3). | Motor command is stopped too early before walker can be fully actuated (C4).
Brake Torque Commands (E) | Brake commands are not provided (E1). | Incorrect braking torque applied to wheels. Brakes are abruptly applied at too high a speed (E2). | Brakes react to commands too early or too late (E3). | Brakes stop braking when they should not (E4).
Wheel Torque Commands (F) | Torque command for wheels is not provided (F1). | Incorrect torque is applied to wheels. Too high of a torque is produced by the motors (F2). | Motors react to commands too early or too late (F3). | Motors stop applying torque when they should not (F4).
User Selects Target Location (G, L) | User does not select a target location when needed (G1). | User selects an inappropriate target location (G2). | User selects a target location out of sequence (G3). | N/A.
Retrieving Wheel Movement Data (H) | Sensor does not read a wheel’s movement data (H1). | Sensor reads incorrect wheel movement data based on current walker state (H2). | Sensor reads wheel movement data too early or too late (H3). | Sensor data acquisition of wheel movement data stopped too soon (H4).
Retrieving Proximity Data (I) | Proximity sensor does not read data (I1). | Proximity sensor reads incorrect data based on current walker state (I2). | Proximity sensor reads data too early or too late (I3). | Sensor data acquisition proximity data stopped too soon (I4).
Retrieving Depth Image Data (J) | Depth image sensor does not read data (J1). | Depth image sensor reads incorrect data based on current walker state (J2). | Depth image sensor reads data too early or too late (J3). | Sensor data acquisition of depth image data stopped too soon (J4).
Retrieving Walker Pose within Room Map (K) | Sensor does not read walker’s pose within room map (K1). | Sensor reads incorrect walker pose within room map based on current walker position (K2). | Sensor reads walker pose within room map data too early or too late resulting in out of sequence acquisition (K3). | Sensor data acquisition of walker pose within room map stopped too soon (H4).
Converting Sensor Data into Walker State Information (M) | System does not convert sensor data into walker state or converts to an incorrect format (M1). | System incorrectly converts sensor data into an incorrect walker state (M2). | System converts sensor data into walker state information too early or too late (M3). | System conversion of sensor data into walker state information is stopped abruptly (M4).
Converting User Input to Target Information (N) | System does not convert selected user target or converts to an incorrect format (N1). | System incorrectly converts selected user target into an incorrect location (N2). | System converts user selected target into target location too early or too late (N3). | System conversion of user selected target into target location is stopped abruptly (N4).

## 3.2 STPA - Manual Assist

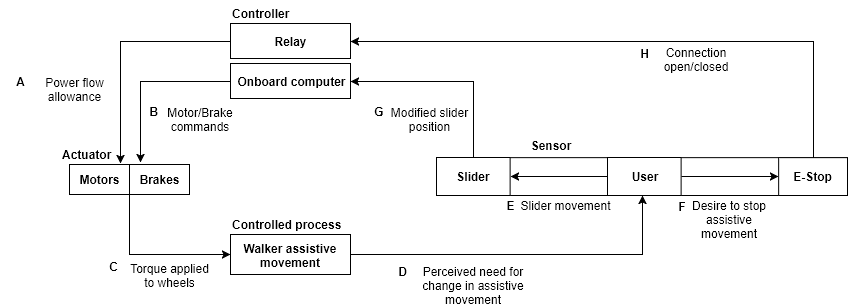
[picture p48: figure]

Figure 3 - STPA for Manual Assist

### 3.2.1 Control Action Hazards

Power Flow Allowance Hazards (A):

- Incorrect allowance
- Timing of change in signal

Motor/Brake Commands Hazards (B):

- Invalid commands sent
- Incorrect commands sent
- Incorrect command instruction timing
- Command exceeds capabilities of actuator

Torque Applied to Wheels Hazards (C):

- Incorrect torque applied
- Operational delays

Perceived Need for Change in Assistive Movement Hazards (D):

- Incorrect change perceived
- Delay in perception of change

Slider Movement Hazards (E):

- Component failure or wear
- Delay in movement

Desire to Stop Assistive Movement Hazards (F):

- Timing of action incorrect
- E-Stop pressed accidentally
- Component failure

Modified Slider Position Hazards (G):

- Incorrect status signal timing
- Incorrect status value sent
- Invalid status value sent

Connection Open/Closed Hazards (H):

- Incorrect status signal timing
- Incorrect status sent

### 3.2.2 STPA Hazard Analysis

Table 7 - STPA Hazard Analysis (Manual Assist)

Control Action | Category 1 (A control action required for safety is not provided or not followed) | Category 2 (An unsafe control action is provided that leads to a hazard) | Category 3 (A potentially safe control action is provided too early, too late, or out of sequence) | Category 4 (A safe control action is stopped too soon)
Power flow allowance (A) | Power flow allowance does not change when relay receives ‘signal’ from E-stop to cut power (A1). | N/A. | Allowance changes too late after E-stop press (A3). | The relay allows power flow to the system even when the E-stop button is pressed (A4).
Motor/Brake commands (B) | Motor and brake commands not followed. Motor and brake commands that cannot be actuated are sent. Commands are not sent at all (B1). | Commands that include the motors and brakes actuating at the same time are sent. Motor torque commands that are too high are sent (B2). | The motor/brake commands are sent out too late. Motor and brake commands are mixed up (B3). | Command to brake is stopped abruptly. Command for motor actuation is stopped abruptly (B4).
Torque applied to wheels (C) | Incorrect torque applied by motor. Brakes not correctly applying torque to wheels. (C1) | Brakes not applying correct amount of torque to wheels. Too high a torque is produced by the motors. Brakes are abruptly applied at too high a speed (C2) | Motors or brakes react to commands too late. Motors and brakes actuate at same time due to incorrect commands (C3) | Brakes stop braking when they should not. Motors stop applying torque when they should not (C4)
Perceived need for change in assistive movement (D) | No change provided by user (D1). | An incorrect change is perceived by user (D2). | Perception of change is delayed by user (D3). | N/A.
Slider movement (E) | Slider not moved in relation to desired change in assistive movement (E1). | Slider moved incorrectly in relation to desired change in assistive movement. Slider moved too quickly (E2). | Slider movement is delayed in relation to perception of change in assistive movement (C3). | Slider movement stopped or modified before change in movement is implemented (C4).
Desire to stop assistive movement (F) | E-Stop does not register press from user due to mechanical failure (F1). | E-Stop pressed accidentally by user (F2). | E-Stop is pressed too late by user (F3). | E-Stop releases when it should not (F4).
Modified slider position (G) | Position is not transmitted sent at all (G1). | Position transmitted is incorrect. Position transmitted is invalid (G2). | Position is sent too late (G3). | N/A.
Connection open/closed (H) | The state of the connection is not correctly set by the E-Stop (H1). | N/A. | The connection is not closed or opened fast enough (H3). | The connection is opened abruptly when it should be closed, or vice versa (H4).

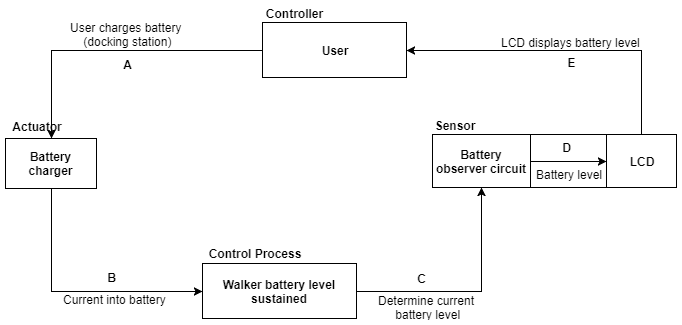
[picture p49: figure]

## 3.3 STPA - Battery Level

Figure 4 - STPA for Battery Level

### 3.3.1 Control Action Hazards

User Charges Battery Hazards (A):

- Incorrect connection to docking station

Current into Battery Hazards (B)

- Incorrect current value to battery
- Incorrect battery current supply timing

Determine Current Battery Level Hazards (C):

- Invalid determination of current battery level
- Valid, but incorrect determination of current battery level
- Incorrect determination of current battery level timing

Battery Level Sent to LCD Hazards (D):

- Operational delays
- Same as C

LCD Displays Battery Level Hazards (E):

- Operational delays
- Same as C

### 3.3.2 STPA Hazard Analysis

Table 8 - STPA Hazard Analysis (Battery Level)

Control Action | Category 1 (A control action required for safety is not provided or not followed) | Category 2 (An unsafe control action is provided that leads to a hazard) | Category 3 (A potentially safe control action is provided too early, too late, or out of sequence) | Category 4 (A safe control action is stopped too soon)
User Moving the Walker to Charge the Battery (A) | User does not put walker back to docking station to charge the battery (A1). | User puts the walker to an incorrect location to charge the battery (A2). | User puts walker to docking station to charge battery too late (A3). | User putting walker to docking station to charge battery stopped abruptly (A4).
Determining the Current Needed to Charge the Battery (B) | Battery charger does not send current to charge the battery (B1). | Battery charger sends too little or too much current to charge the battery (B2). | Battery charge sends current to charge battery too early or too late (B3). | Battery charger stops charging battery abruptly (B4).
Determining the Current Battery Level on the Walker (C, D) | System does not determine current battery level (C1). | System determines the incorrect value for current battery level (C2). | System determines current battery level too late (C3). | System determination of current battery level is stopped too soon (C4).
Current Battery Level Shown to User on LCD (E) | LCD is not provided with a battery level, or provided incorrectly (E1). | Current battery level provided to LCD is incorrect (too high or too low) (E2). | Current battery level is provided and shown on LCD too late (E3). | Current battery level stops from being displayed on the LCD (E4).

# 4 Safety Considerations

The safety of the user is one of the most important aspects of the SmartWalker, therefore, it is important that that any component that could harm the user directly be considered. Certain functions are very dependent on the hardware working correctly without obstruction. The system must be able to analyze and either adapt properly or defuse the situation, pertaining to the system, from escalating catastrophically. The following is a list of some of the high-risk hazards and ways to mitigate the risk of them occurring. These solutions will not necessarily be implemented, however, feasible solutions for these hazards will be implemented to ensure a safe system.

## 4.1 Collision Hazard

Issue

The risk of the SmartWalker colliding with an object or person can range from high to catastrophic, during autonomous mode. The SmartWalker is intended to work in a hospital environment where there is a lot of sensitive and expensive equipment and injured/ill patients. Compared to other autonomous systems, such as a Roomba, a simple bump into the wall or furniture would not lead to high to catastrophic consequences. It is vital that the SmartWalker avoid collision as much as possible.

Solution

The solution would be to minimize if not eliminate the risk of this hazard occurring. Several small steps in product development process need to be taken into consideration

## 4.2 Power Supply

Issues

1. Not enough power for the system
2. Not charging correctly

Solutions

1. Several steps can be taken to mitigate the issue of not having enough power. Display the battery level to the user so they are aware of their current state, warn the user when the battery level reaches a certain point, and then power down safely (gracefully) when the battery reaches a critical level. Unlock the brakes when there is no power so that the walker can be moved to a safe location.
2. The best solution would be for the walker to run a self-diagnosis when it senses the walker docked and plugged in to charge, the battery level less than 100%, and the battery not being charged. After the diagnosis, the walker would send a message to the user of the issue based on results. An alternate solution would be for the walker to send a warning to either the users phone or the HMI that the battery is not charging. The user can then investigate further if there is an issue of not.

## 4.3 Sensors

Issues

1. Sensor is blocked and is unable to properly take readings
2. Sensor is blocked and taking incorrect readings
3. Sensor is damaged and is unable to properly take readings
4. Sensor is damaged and taking incorrect readings

Solutions

1. Display warning to user on HMI. User to remove blockage.
2. If the user notices that the walker is not working properly, they can use the emergency stop button.
3. Display warning to user on HMI. User to have sensor repaired or replaced.
4. If the user notices that the walker is not working properly, they can use the emergency stop button.

## 4.4 Electronic Part Failure

Electronic parts in this case is any part used in the electrical subsystem of the SmartWalker that is not the power supply or a sensor.

Issues

1. Loss of Control
2. Exposed or broken wires

Solutions

1. Make an emergency stop available to the user. The stop option will be applied by the user when there is an emergency involving the SmartWalker and it needs to be immediately be stopped (apply brakes/stop motors, send message to user of emergency button being applied, cease all functions and restart upon emergency stop being disabled).
2. Construct the SmartWalker to hide/cover all wiring and electronics. Leave an access panel for troubleshooting issues. Since the environment of the walker is within a hospital the cover does not need to be weatherproof.

# 5 Conclusion

An important part of product development is completing a hazard analysis to ensure that the system is safe for use. Using the STPA process we have noted several hazards both major and minor that are present in the system. While we cannot eliminate all the hazards we can reduce the risk of these hazards from occurring. Each hazard is referenced against the System Requirements document of the SmartWalker so that the project is accommodative and adherent to the possible hazards per component. Any changes in requirements will be followed by updated system and component diagrams to adhere in order to adhere to said changes.

MODERN MOBILITY HAZARD ANALYSIS DOCUMENT Doc: DOC0005 Rev: F

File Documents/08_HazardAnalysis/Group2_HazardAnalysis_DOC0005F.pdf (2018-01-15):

MODERN MOBILITY
HAZARD ANALYSIS DOCUMENT

Doc: DOC0005
Rev: F

# HAZARD ANALYSIS DOCUMENT

MECHATRONICS 4TB6
GROUP 2
NATHAN FUJIMOTO | 1224348
PRAKHAR GARG | 1204351
JOSH GILMOUR | 1402325
AARON JASS | 1218859
TYLER JASS | 1218857
FAUZIA KHANUM | 1209252
JACK LIU | 1215056
GAGAN SINGH | 1306242

HAZARD ANALYSIS DOCUMENT

Rev: F

## Table of Contents

1 Introduction | 5
2 Overview | 6
2.1 Component Overview | 6
2.2 Component Description | 8
2.2.1 Navigation Module | 8
2.2.2 Human Interface Module | 8
2.2.3 Walker Interface Module | 8
2.2.4 Drive Modules | 8
2.3 System Variables | 9
3 STPA | 14
3.1 STPA - Navigation | 15
3.1.1 Control Action Hazards | 16
3.1.2 STPA Hazard Analysis | 17
3.2 STPA - Manual Assist | 20
3.2.1 Control Action Hazards | 21
3.2.2 STPA Hazard Analysis | 22
3.3 STPA - Battery Level | 24
3.3.1 Control Action Hazards | 25
3.3.2 STPA Hazard Analysis | 25
4 Safety Considerations | 27
4.1 Collision Hazard | 27
4.2 Power Supply | 27
4.3 Sensors | 28
4.4 Electronic Part Failure | 28
5 Conclusion | 29

HAZARD ANALYSIS DOCUMENT

Rev: F

## Table of Figures

Figure 1 - High Level Module Diagram | 7
Figure 2 - STPA for Navigation Diagram | 15
Figure 3 - STPA for Manual Assist | 20
Figure 4 - STPA for Battery Level | 24

## Table of Tables

Table 1 - System Variable Prefixes | 9
Table 2 - Monitored Variables | 9
Table 3 - Controlled Variables | 11
Table 4 - Input Variables | 11
Table 5 - Output Variables | 13
Table 6 - STPA Hazard Analysis (Navigation) | 17
Table 7 - STPA Hazard Analysis (Manual Assist) | 22
Table 8 - STPA Hazard Analysis (Battery Level) | 25

HAZARD ANALYSIS DOCUMENT

Rev: F

## Revision History

Rev | Author(s) | Description of Change | Peer Reviewed | Date
- | T.Jass | Original Document | A.Jass N.Fujimoto | 04-Jan-2018
A | N.Fujimoto | Listing components | F. Khanum | 04-Jan-2018
B | J.Gilmor F.Khanum A.Jass T.Jass | Began STPA Hazard Analysis Began List of Safety Consideration Adding Component descriptions | A.Jass T.Jass | 05-Jan-2018
C | A.Jass T.Jass J.Liu | Developing component overview and component descriptions Added Introduction | N.Fujimoto J.Gilmour | 06-Jan-2018
D | N.Fujimoto J.Gilmor | Added STPA diagrams Added STPA Hazards, Hazard Table | F. Khanum | 08-Jan-2018
E | N.Fujimoto J.Gilmor F. Khanum | Completed initial draft of STPA Hazard Analysis Safety Considerations | T.Jass | 09-Jan-2018
F | T.Jass N.Fujimoto | Added System variable tables and formatted document | A.Jass | 11-Jan-2018

HAZARD ANALYSIS DOCUMENT

Rev: F

## 1 Introduction

The purpose of this document is to outline the components, safety considerations, and hazards for the SmartWalker. The first part of this document will provide an overview of all the various hardware and software components, along with a brief description of each component. The second part will list the safety considerations for each component as well as detail how these safety considerations will be implemented. Finally, a comprehensive analysis will be conducted of potential hazards through a Systems-Theoretic Process Analysis (STPA) approach for each of our controlled processes. In this diagram, a list of potential hazards will be compiled by analyzing the potential interaction failures in the components, and in the environment, and steps to mitigate these failures will be discussed.

HAZARD ANALYSIS DOCUMENT

Rev: F

## 2 Overview

### 2.1 Component Overview

The following diagram gives a high-level overview of the SmartWalker system from the inputs into the different modules to outputs per module. As seen below the system is made of four modules: the navigation module, the human interface module, the walker interface module, and the drive module. These modules will aid in finding and describing the different hazards present in the system.

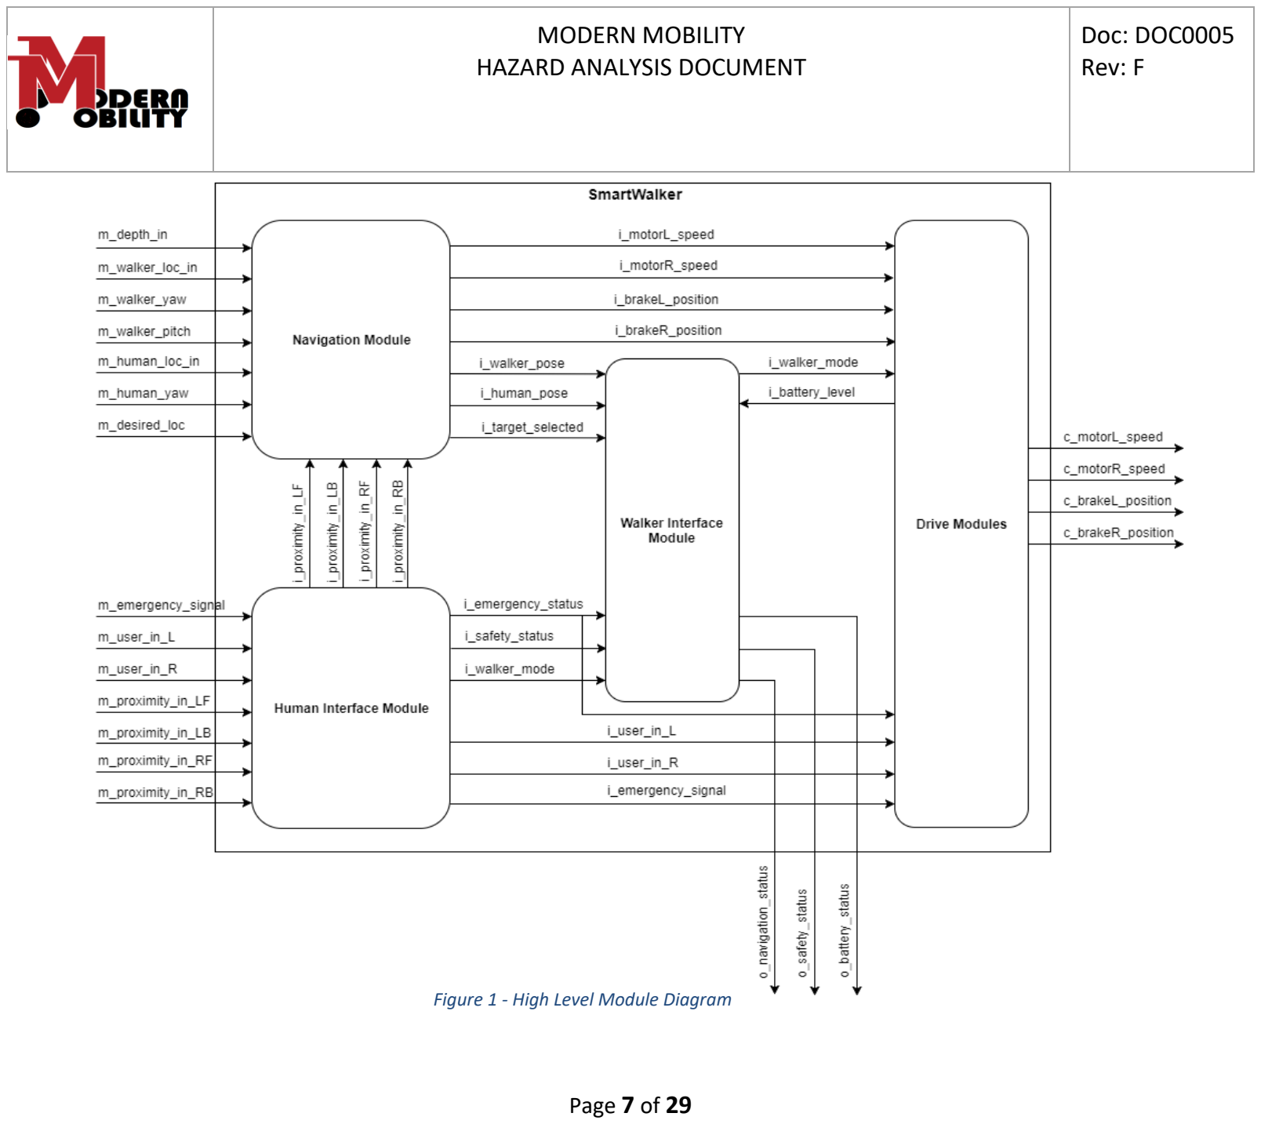
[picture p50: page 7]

MODERN MOBILITY
HAZARD ANALYSIS DOCUMENT

Doc: DOC0005
Rev: F

Page 7 of 29

Figure 1 - High Level Module Diagram

HAZARD ANALYSIS DOCUMENT

Rev: F

### 2.2 Component Description

A description of each component (or module) is given below.

### 2.2.1 Navigation Module

This module is the main navigation module which autonomously moves the SmartWalker between two locations within a room. This module directly takes in the main navigation depth image sensor data, mapping data and user target data, while receiving information from the human interface module about manual assistive needs and proximity to other objects. It passes motor and brake commands to the drive module and passes navigation variables to the walker interface module.

### 2.2.2 Human Interface Module

This module contains the human-machine interfaces that directly get inputs from the user while in manual use like handle information and the need for emergency braking. In addition, it is connected to proximity data which collects information on approaching objects to the human (and SmartWalker). The proximity information is passed on to the Navigation Module, safety data and emergency inputs are passed on to the Walker Interface Module, and finally the user handle inputs and emergency signal are connected to the Drive Module.

### 2.2.3 Walker Interface Module

The Walker Interface Module displays information of the walker’s statuses to user while all modes. It takes in navigation information to output a navigation status to the user, as well as takes emergency status and safety status information to be displayed to the user’s mobile device and walker screen depending on the mode of operation of the SmartWalker.

### 2.2.4 Drive Modules

This module takes in the motor/brake commands outputted by the Master Control Module and executes them by actuating the motors/brakes. It also receives the desired user speed (or braking request) and emergency request and executes them in real-time by again actuating the motors/brakes.

HAZARD ANALYSIS DOCUMENT

Rev: F

### 2.3 System Variables

The following are several tables specifying the system’s different variables, a legend is included below providing the meaning of the prefixes:

Table 1 - System Variable Prefixes

Prefix | Meaning | Description
m | Monitored | Variables that store information from sensors about the physical environment.
c | Controlled | Variables that store information to be outputted to actuators.
i | Input | Purely software variable that is an input to a software module.
o | Output | Variable that is an output determined by a software module.

Table 2 - Monitored Variables

Variable | Description | Units | Range
m_battery_lvl | Power level of battery. | Battery Sustain of Charge (%) | [0, 100]
m_battery_rel | Reliability of the battery. | Battery Health (%) | [0, 100]
m_proximity_in_LF | Proximity to any objects in the environment (front-left side). | Distance (cm) | [0, 500]
m_proximity_in_RF | Proximity to objects in the environment (front-right side). | Distance (cm) | [0, 500]
m_proximity_in_LB | Proximity to any objects in the environment (back-left side). | Distance (cm) | [0, 500]
m_proximity_in_RB | Proximity to objects in the environment (back-right side). | Distance (cm) | [0, 500]
m_depth_in | Depth of the upcoming ground | Distance (cm) | [-100, 0]

HAZARD ANALYSIS DOCUMENT

Rev: F

| with respect to the bottom of the walker.
m_walker_yaw | Orientation of the walker (yaw) with respect to the walker’s z-axis. | Angle (deg) | [-180, 180]
m_walker_pitch | Orientation of the walker (pitch) with respect to the walker’s y-axis. | Angle (deg) | [-45, 45]
m_walker_loc_out | Global location of the walker. | [Longitude (deg), Latitude (deg)] | [-180, 180; -90,90]
m_walker_loc_in | Location of the walker inside the patient room, with respect to a preset coordinate system. | [x,y] on room map | [0, 100; 0, 100]
m_human_loc_in | Location of the human based on their phone, with respect to a preset coordinate system. | [x, y] on room map | [0, 100; 0, 100]
m_human_yaw | Orientation of the human (yaw) with respect to the human’s z-axis. | Angle (deg) | [-45, 45]
m_desired_loc | User selected desired location for the walker in autonomous mode | Enum (states) | GoDocking, GoHuman
m_dock_aligned | Walker is physically aligned with the docking station | Boolean | 0, 1
m_user_in_L | Desired forward assisted movement for the user, for the left motor. | Custom | [-100,100]
m_user_in_R | Desired forward assisted | Custom | [-100,100]

HAZARD ANALYSIS DOCUMENT

Rev: F

| movement for the user, for the left motor.
m_emergency_signal | Signal for monitoring an emergency situation. | Boolean | 0, 1

Table 3 - Controlled Variables

Variable | Description | Units | Range
c_motorL_speed | Left motor speed. | Angular velocity ( deg/s) | [0, 50]
c_motorR_speed | Right motor speed. | Angular velocity (deg/s) | [0, 50]
c_brakeL_position | Left brake position. | Brake Position (%) | [0, 100]
c_brakeR_position | Right brake position. | Brake Position (%) | [0, 100]
c_charge_walker | Charge the walker. | Boolean | 0, 1
c_dock_connected | Walker physically connected to the docking station. | Boolean | 0, 1

Table 4 - Input Variables

Variable | Description | Data Type | Range
i_motorL_speed | Left wheel motor forward speed command. | 32 bit float | [0, 2]
i_motorR_speed | Right wheel motor forward speed command. | 32 bit float | [0, 2]

HAZARD ANALYSIS DOCUMENT

Rev: F

i_brakeL_position Left brake motor position
command.
32 bit float | [0, 1]
i_brakeR_position | Right brake motor position command. | 32 bit float | [0, 1]
i_walker_pose | Walker’s position and orientation within room map. | 32 bit float array (x, y, z, θ) | [0, 100; 0, 100; 0, 100; -180, 180]
i_human_pose | User’s position and orientation within room map. | 32 bit float array (x, y, z, θ) | [0, 100; 0, 100; 0, 100; -180, 180]
i_target_selected | User’s desired navigation target for walker. | Enum | USER, DOCK
i_proximity_in_LF | Proximity to objects (left-front side). | 32 bit float | [0, 500]
i_proximity_in_LB | Proximity to objects (left-back side). | 32 bit float | [0, 500]
i_proximity_in_RB | Proximity to objects (right-front side). | 32 bit float | [0, 500]
i_proximity_in_RF | Proximity to objects (right-front side). | 32 bit float | [0, 500]
i_emergency_status | Walker’s status of immediate emergencies. | Enum | NON_EMER, EMER
i_safety_status | Walker’s status of unsafe scenarios approaching. | Enum | SAFE, UNSAFE
i_walker_mode | The mode of operation. | Enum | INIT, MAN, AUTO
i_user_input_R | Requested forward assisted movement for the user, for the left motor. | 16 bit uint | [0, 1024]

HAZARD ANALYSIS DOCUMENT

Rev: F

i_user_input_L | Requested forward assisted
movement for the user, for the right motor.
16 bit uint | 0, 1024]
i_emergency_signal | Signal indicating an emergency
situation.
Boolean | 0, 1

Table 5 - Output Variables

Variable | Description | Data Type | Range
o_navigation_status | Current state of the Walker’s navigation process | Enum | IDLE, INIT, TRAN, FINE
o_safety_status | Current state of the overall system’s safety | Enum | UNSAFE, SAFE

HAZARD ANALYSIS DOCUMENT

Rev: F

## 3 STPA

In order to properly identify a comprehensive list of hazards for the SmartWalker project, a STPA Hazard Analysis was completed of the main controlled processes of the walker. For each of the main controlled processes, a NRC diagram was created for each to outline the appropriate control actions. Next general hazards were outlined for each and then finally hazards were organized by the four STPA categories.

MODERN MOBILITY
HAZARD ANALYSIS DOCUMENT

Doc: DOC0005
Rev: F

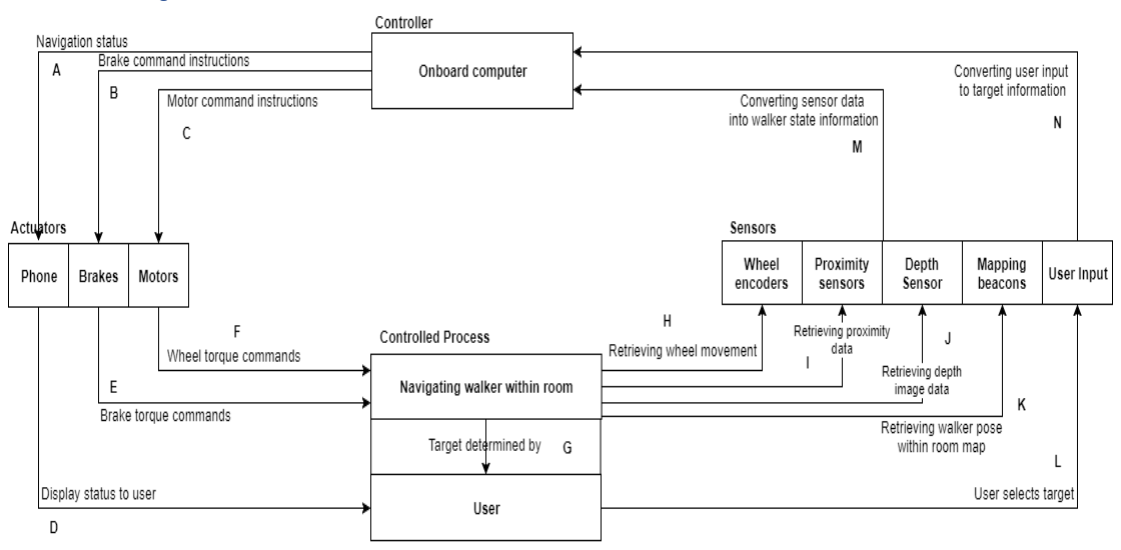
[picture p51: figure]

Page 15 of 29

### 3.1 STPA - Navigation

Figure 2 - STPA for Navigation Diagram

HAZARD ANALYSIS DOCUMENT

Rev: F

### 3.1.1 Control Action Hazards

Navigation Status Hazards (A):
- Incorrect status sent
- Incorrect status signal timing

Brake Command Instructions Hazards (B):
- Incorrect command sent
- Incorrect command instruction timing

Motor Command Instructions Hazards (C):
- Incorrect command sent
- Incorrect command instruction timing

Display Status to User Hazards (D):
- Operational delays
- Same as A

Brake Torque Commands Hazards (E):
- Operational delays
- Same as B

Wheel Torque Commands Hazards (F):
- Operational delays
- Same as F

Target Received Hazards (G)
- Invalid user target selection received
- Valid but incorrect user target selection received
- Incorrect user target selection timing

Retrieving Wheel Movement Hazards (H):
- Invalid wheel movement data received
- Valid but incorrect wheel movement data received
- Incorrect wheel movement data retrieval timing

Retrieving Proximity Data Hazards (I):
- Invalid proximity data received
- Valid but incorrect proximity data received
- Incorrect proximity data retrieval timing

HAZARD ANALYSIS DOCUMENT

Rev: F

Retrieving Depth Image Data Hazards (J):
- Invalid depth image data received
- Valid but incorrect depth image data received
- Incorrect depth image data retrieval timing

Retrieving Walker Pose within Room Map (K):
- Invalid walker pose within room map received
- Valid but incorrect walker pose within room map received
- Incorrect walker pose within room map retrieval timing

User Selects Target (L):
- Same as G

Converting Sensor Data into Walker State Information (M):
- Operational Delays
- Same as G, H, I, J, L

Converting User Input to Target Information Hazards (N):
- Operational Delays
- Same as G

### 3.1.2 STPA Hazard Analysis

Table 6 - STPA Hazard Analysis (Navigation)

Control Action | Category 1 (A control action required for safety is not provided or not followed) | Category 2 (An unsafe control action is provided that leads to a hazard) | Category 3 (A potentially safe control action is provided too early, too late, or out of sequence) | Category 4 (A safe control action is stopped too soon)
Sending Navigation Status (A, D) | System does not send navigation status when needed for the user (A1). | System sends that the walker has arrived when walker has yet to arrive (and vice-versa) (A2). | System sends walker has arrived too early or too late to the user (A3). | N/A.
Sending Brake Command Instructions (B, E) | Brake commands are not sent when requested or with | System sends an inappropriate brake command | Brake command is sent too early or too late which | Brake command is stopped too early before walker can

HAZARD ANALYSIS DOCUMENT

Rev: F

| an incorrect message format (B1). | for current navigation needs (B2). | forces navigation position out of sync (B3). | be fully actuated (B4).
Sending Motor Command Instructions (C) | Motor commands are not sent when requested or with an incorrect message format (C1). | System sends an inappropriate motor command for current navigation needs (C2). | Motor command is sent too early or too late which forces navigation position out of sync (C3). | Motor command is stopped too early before walker can be fully actuated (C4).
Brake Torque Commands (E) | Brake commands are not provided (E1). | Incorrect braking torque applied to wheels. Brakes are abruptly applied at too high a speed (E2). | Brakes react to commands too early or too late (E3). | Brakes stop braking when they should not (E4).
Wheel Torque Commands (F) | Torque command for wheels is not provided (F1). | Incorrect torque is applied to wheels. Too high of a torque is produced by the motors (F2). | Motors react to commands too early or too late (F3). | Motors stop applying torque when they should not (F4).
User Selects Target Location (G, L) | User does not select a target location when needed (G1). | User selects an inappropriate target location (G2). | User selects a target location out of sequence (G3). | N/A.
Retrieving Wheel Movement Data (H) | Sensor does not read a wheel’s movement data (H1). | Sensor reads incorrect wheel movement data based on current walker state (H2). | Sensor reads wheel movement data too early or too late (H3). | Sensor data acquisition of wheel movement data stopped too soon (H4).
Retrieving Proximity Data (I) | Proximity sensor does not read data (I1). | Proximity sensor reads incorrect data based on current walker state (I2). | Proximity sensor reads data too early or too late (I3). | Sensor data acquisition proximity data stopped too soon (I4).
Retrieving Depth | Depth image | Depth image | Depth image | Sensor data

HAZARD ANALYSIS DOCUMENT

Rev: F

Image Data (J) | sensor does not read data (J1). | sensor reads incorrect data based on current walker state (J2). | sensor reads data too early or too late (J3). | acquisition of depth image data stopped too soon (J4).
Retrieving Walker Pose within Room Map (K) | Sensor does not read walker’s pose within room map (K1). | Sensor reads incorrect walker pose within room map based on current walker position (K2). | Sensor reads walker pose within room map data too early or too late resulting in out of sequence acquisition (K3). | Sensor data acquisition of walker pose within room map stopped too soon (H4).
Converting Sensor Data into Walker State Information (M) | System does not convert sensor data into walker state or converts to an incorrect format (M1). | System incorrectly converts sensor data into an incorrect walker state (M2). | System converts sensor data into walker state information too early or too late (M3). | System conversion of sensor data into walker state information is stopped abruptly (M4).
Converting User Input to Target Information (N) | System does not convert selected user target or converts to an incorrect format (N1). | System incorrectly converts selected user target into an incorrect location (N2). | System converts user selected target into target location too early or too late (N3). | System conversion of user selected target into target location is stopped abruptly (N4).

MODERN MOBILITY
HAZARD ANALYSIS DOCUMENT

Doc: DOC0005
Rev: F

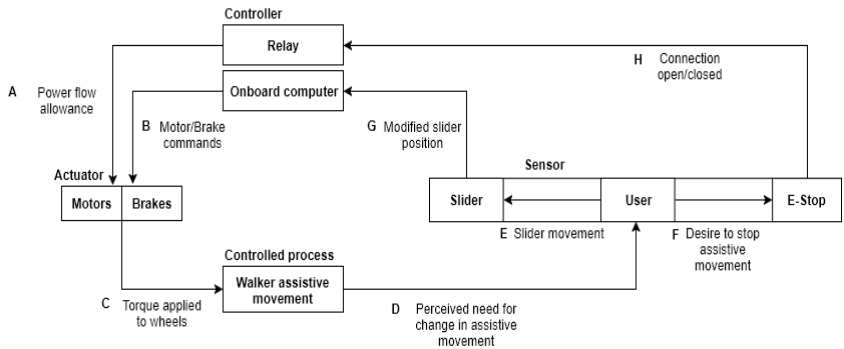
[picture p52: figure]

Page 20 of 29

### 3.2 STPA - Manual Assist

Figure 3 - STPA for Manual Assist

HAZARD ANALYSIS DOCUMENT

Rev: F

### 3.2.1 Control Action Hazards

Power Flow Allowance Hazards (A):
- Incorrect allowance
- Timing of change in signal

Motor/Brake Commands Hazards (B):
- Invalid commands sent
- Incorrect commands sent
- Incorrect command instruction timing
- Command exceeds capabilities of actuator

Torque Applied to Wheels Hazards (C):
- Incorrect torque applied
- Operational delays

Perceived Need for Change in Assistive Movement Hazards (D):
- Incorrect change perceived
- Delay in perception of change

Slider Movement Hazards (E):
- Component failure or wear
- Delay in movement

Desire to Stop Assistive Movement Hazards (F):
- Timing of action incorrect
- E-Stop pressed accidentally
- Component failure

Modified Slider Position Hazards (G):
- Incorrect status signal timing
- Incorrect status value sent
- Invalid status value sent

Connection Open/Closed Hazards (H):
- Incorrect status signal timing
- Incorrect status sent

HAZARD ANALYSIS DOCUMENT

Rev: F

### 3.2.2 STPA Hazard Analysis

Table 7 - STPA Hazard Analysis (Manual Assist)

Control Action | Category 1 (A control action required for safety is not provided or not followed) | Category 2 (An unsafe control action is provided that leads to a hazard) | Category 3 (A potentially safe control action is provided too early, too late, or out of sequence) | Category 4 (A safe control action is stopped too soon)
Power flow allowance (A) | Power flow allowance does not change when relay receives ‘signal’ from E-stop to cut power (A1). | N/A. | Allowance changes too late after E-stop press (A3). | The relay allows power flow to the system even when the E-stop button is pressed (A4).
Motor/Brake commands (B) | Motor and brake commands not followed. Motor and brake commands that cannot be actuated are sent. Commands are not sent at all (B1). | Commands that include the motors and brakes actuating at the same time are sent. Motor torque commands that are too high are sent (B2). | The motor/brake commands are sent out too late. Motor and brake commands are mixed up (B3). | Command to brake is stopped abruptly. Command for motor actuation is stopped abruptly (B4).
Torque applied to wheels (C) | Incorrect torque applied by motor. Brakes not correctly applying torque to wheels. (C1) | Brakes not applying correct amount of torque to wheels. Too high a torque is produced by the motors. Brakes are abruptly applied at too high a speed (C2) | Motors or brakes react to commands too late. Motors and brakes actuate at same time due to incorrect commands (C3) | Brakes stop braking when they should not. Motors stop applying torque when they should not (C4)
Perceived need | No change | An incorrect | Perception of | N/A.

HAZARD ANALYSIS DOCUMENT

Rev: F

for change in assistive movement (D) | provided by user (D1). | change is perceived by user (D2). | change is delayed by user (D3).
Slider movement (E) | Slider not moved in relation to desired change in assistive movement (E1). | Slider moved incorrectly in relation to desired change in assistive movement. Slider moved too quickly (E2). | Slider movement is delayed in relation to perception of change in assistive movement (C3). | Slider movement stopped or modified before change in movement is implemented (C4).
Desire to stop assistive movement (F) | E-Stop does not register press from user due to mechanical failure (F1). | E-Stop pressed accidentally by user (F2). | E-Stop is pressed too late by user (F3). | E-Stop releases when it should not (F4).
Modified slider position (G) | Position is not transmitted sent at all (G1). | Position transmitted is incorrect. Position transmitted is invalid (G2). | Position is sent too late (G3). | N/A.
Connection open/closed (H) | The state of the connection is not correctly set by the E-Stop (H1). | N/A. | The connection is not closed or opened fast enough (H3). | The connection is opened abruptly when it should be closed, or vice versa (H4).

MODERN MOBILITY
HAZARD ANALYSIS DOCUMENT

Doc: DOC0005
Rev: F

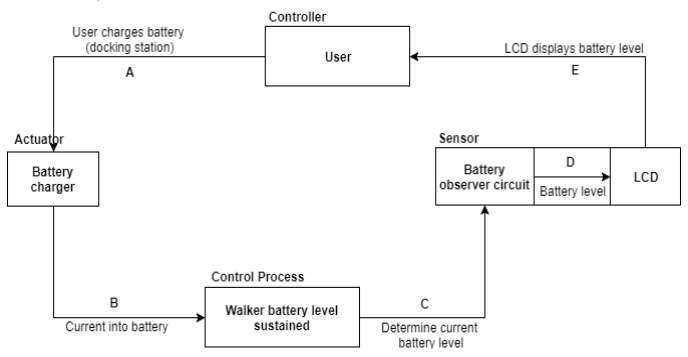
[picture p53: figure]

Page 24 of 29

### 3.3 STPA - Battery Level

Figure 4 - STPA for Battery Level

HAZARD ANALYSIS DOCUMENT

Rev: F

### 3.3.1 Control Action Hazards

User Charges Battery Hazards (A):
- Incorrect connection to docking station

Current into Battery Hazards (B)
- Incorrect current value to battery
- Incorrect battery current supply timing

Determine Current Battery Level Hazards (C):
- Invalid determination of current battery level
- Valid, but incorrect determination of current battery level
- Incorrect determination of current battery level timing

Battery Level Sent to LCD Hazards (D):
- Operational delays
- Same as C

LCD Displays Battery Level Hazards (E):
- Operational delays
- Same as C

### 3.3.2 STPA Hazard Analysis

Table 8 - STPA Hazard Analysis (Battery Level)

Control Action | Category 1 (A control action required for safety is not provided or not followed) | Category 2 (An unsafe control action is provided that leads to a hazard) | Category 3 (A potentially safe control action is provided too early, too late, or out of sequence) | Category 4 (A safe control action is stopped too soon)
User Moving the Walker to Charge the Battery (A) | User does not put walker back to docking station to charge the battery (A1). | User puts the walker to an incorrect location to charge the battery (A2). | User puts walker to docking station to charge battery too late (A3). | User putting walker to docking station to charge battery stopped abruptly (A4).
Determining the Current Needed to Charge the | Battery charger does not send current to charge | Battery charger sends too little or too much current | Battery charge sends current to charge battery too | Battery charger stops charging battery abruptly

HAZARD ANALYSIS DOCUMENT

Rev: F

Battery (B) | the battery (B1). | to charge the battery (B2). | early or too late (B3). | (B4).
Determining the Current Battery Level on the Walker (C, D) | System does not determine current battery level (C1). | System determines the incorrect value for current battery level (C2). | System determines current battery level too late (C3). | System determination of current battery level is stopped too soon (C4).
Current Battery Level Shown to User on LCD (E) | LCD is not provided with a battery level, or provided incorrectly (E1). | Current battery level provided to LCD is incorrect (too high or too low) (E2). | Current battery level is provided and shown on LCD too late (E3). | Current battery level stops from being displayed on the LCD (E4).

HAZARD ANALYSIS DOCUMENT

Rev: F

## 4 Safety Considerations

The safety of the user is one of the most important aspects of the SmartWalker, therefore, it is important that that any component that could harm the user directly be considered. Certain functions are very dependent on the hardware working correctly without obstruction. The system must be able to analyze and either adapt properly or defuse the situation, pertaining to the system, from escalating catastrophically. The following is a list of some of the high-risk hazards and ways to mitigate the risk of them occurring. These solutions will not necessarily be implemented, however, feasible solutions for these hazards will be implemented to ensure a safe system.

### 4.1 Collision Hazard

Issue

The risk of the SmartWalker colliding with an object or person can range from high to catastrophic, during autonomous mode. The SmartWalker is intended to work in a hospital environment where there is a lot of sensitive and expensive equipment and injured/ill patients. Compared to other autonomous systems, such as a Roomba, a simple bump into the wall or furniture would not lead to high to catastrophic consequences. It is vital that the SmartWalker avoid collision as much as possible.

Solution

The solution would be to minimize if not eliminate the risk of this hazard occurring. Several small steps in product development process need to be taken into consideration

### 4.2 Power Supply

Issues

1. Not enough power for the system
2. Not charging correctly

Solutions

1. Several steps can be taken to mitigate the issue of not having enough power. Display the battery level to the user so they are aware of their current state, warn the user when the battery level reaches a certain point, and then power down safely (gracefully) when the battery reaches a critical level. Unlock the brakes when there is no power so that the walker can be moved to a safe location.
2. The best solution would be for the walker to run a self-diagnosis when it senses the walker docked and plugged in to charge, the battery level less than 100%, and the battery not being charged. After the diagnosis, the walker would send a message to the user of the issue based on results. An alternate solution would be for the walker to send a warning to either the users phone or the HMI that the battery is not charging. The user can then investigate further if there is an issue of not.

HAZARD ANALYSIS DOCUMENT

Rev: F

### 4.3 Sensors

Issues

1. Sensor is blocked and is unable to properly take readings
2. Sensor is blocked and taking incorrect readings
3. Sensor is damaged and is unable to properly take readings
4. Sensor is damaged and taking incorrect readings

Solutions

1. Display warning to user on HMI. User to remove blockage.
2. If the user notices that the walker is not working properly, they can use the emergency stop button.
3. Display warning to user on HMI. User to have sensor repaired or replaced.
4. If the user notices that the walker is not working properly, they can use the emergency stop button.

### 4.4 Electronic Part Failure

Electronic parts in this case is any part used in the electrical subsystem of the SmartWalker that is not the power supply or a sensor.

Issues

1. Loss of Control
2. Exposed or broken wires
Solutions
1. Make an emergency stop available to the user. The stop option will be applied by the user when there is an emergency involving the SmartWalker and it needs to be immediately be stopped (apply brakes/stop motors, send message to user of emergency button being applied, cease all functions and restart upon emergency stop being disabled).
2. Construct the SmartWalker to hide/cover all wiring and electronics. Leave an access panel for troubleshooting issues. Since the environment of the walker is within a hospital the cover does not need to be weatherproof.

HAZARD ANALYSIS DOCUMENT

Rev: F

## 5 Conclusion

An important part of product development is completing a hazard analysis to ensure that the system is safe for use. Using the STPA process we have noted several hazards both major and minor that are present in the system. While we cannot eliminate all the hazards we can reduce the risk of these hazards from occurring. Each hazard is referenced against the System Requirements document of the SmartWalker so that the project is accommodative and adherent to the possible hazards per component. Any changes in requirements will be followed by updated system and component diagrams to adhere in order to adhere to said changes.

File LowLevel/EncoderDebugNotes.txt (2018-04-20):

Right 
129 - 638 - 128
(509/510)
359 - 1388 - 362
(514.5/513)
 
Left
56 - 571 - 60
(515/511)
61 - 1083 - 54
(511/514.5)

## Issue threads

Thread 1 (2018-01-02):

Add I2C to motor control node

gilmoujw, 2018-01-02:
The code for reading and sending values to the motor control Arduinos must be added to the motor control node

gilmoujw, 2018-01-11:
The software has been written and is awaiting testing. The testing will be done once I can get my Arduino back from those weird PID people.

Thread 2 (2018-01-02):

Add Serial to ultrasound sensor node

gilmoujw, 2018-01-02:
The node that deals with the ultrasound sensors and sliders must have code added to it for communicating over Serial with the arduino. The code only needs to be able to receive messages.

gilmoujw, 2018-01-11:
The communication software has been added to the node. The node is complete.

gilmoujw, 2018-01-11:
Accidentally didn't close the issue

**I am a failure**

gilmoujw, 2018-01-11:
NOT AGAIN

Closed 2018-01-11.

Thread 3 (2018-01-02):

Arduino code for ultrasound sensors

gilmoujw, 2018-01-02:
As per the low voltage wiring diagram, an arduino will be connected to the ultrasound sensors. Code must be written for this arduino that:
- Sets up the pins attached to the ultrasound sensors
- Sets up I2C communication with the PI
- In an **infinite loop**: Reads the value from each ultrasound sensor, converts the reading to meters, and places them in an array of four values. This array should then be sent over I2C to the Pi.
- Sleep the arduino for some reasonable amount of time to ensure we are not constantly sending new readings. 20 ms or something would be reasonable

gilmoujw, 2018-01-07:
Completed and pushed to the git. Needs actual pin values for each sensor set once we have the wiring done, and needs to be integrated with the code that will control the brakes, since both the brakes and ultrasound sensors are to be controlled from one arduino.

Closed 2018-01-07.

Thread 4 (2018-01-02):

Configuration and setup of the differential drive package

gilmoujw, 2018-01-02:
The differential drive package takes the velocity command from the navigation library and splits it into torque commands for each wheel that implements that velocity command. All nodes are already given, but their parameters and the topic names they look for must be configured. The [package page](http://wiki.ros.org/differential_drive) on the ROS wiki gives a sufficient tutorial for accomplishing this.

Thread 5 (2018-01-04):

Transform package configuration

gilmoujw, 2018-01-04:
The transform package must be setup and configured for our use case. There must be transforms for the kinect and ultrasound sensor point cloud as required by the navigation library.

Khanumf, 2018-01-17:
/home/fauziakhanum/catkin_ws/src/robot_setup_tf/src/tf_broadcaster.cpp
/home/fauziakhanum/catkin_ws/src/robot_setup_tf/src/tf_listener.cpp

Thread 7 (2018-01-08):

Arduino PID code

Tylernol2, 2018-01-08:

NathanFujimoto, 2018-01-11:
Completed initial PID code that will go on to the arduino motor controllers. Will have to retest K values for tuning once motors are ready to test with.

gilmoujw, 2018-01-11:
The code is working and so the issue will be closed. Tuning the PID values will be a separate issue.

Closed 2018-01-11.

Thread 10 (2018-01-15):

Add buttons to app and create display for current command

AroJ3, 2018-01-15:
One for each command and have it send the corresponding data

AroJ3, 2018-01-15:
Create module on Rpi that publishes integer value corresponding to command for ROS navigation

AroJ3, 2018-01-16:
This has been implemented, but not yet tested. Will be soon.

Closed 2018-01-18.

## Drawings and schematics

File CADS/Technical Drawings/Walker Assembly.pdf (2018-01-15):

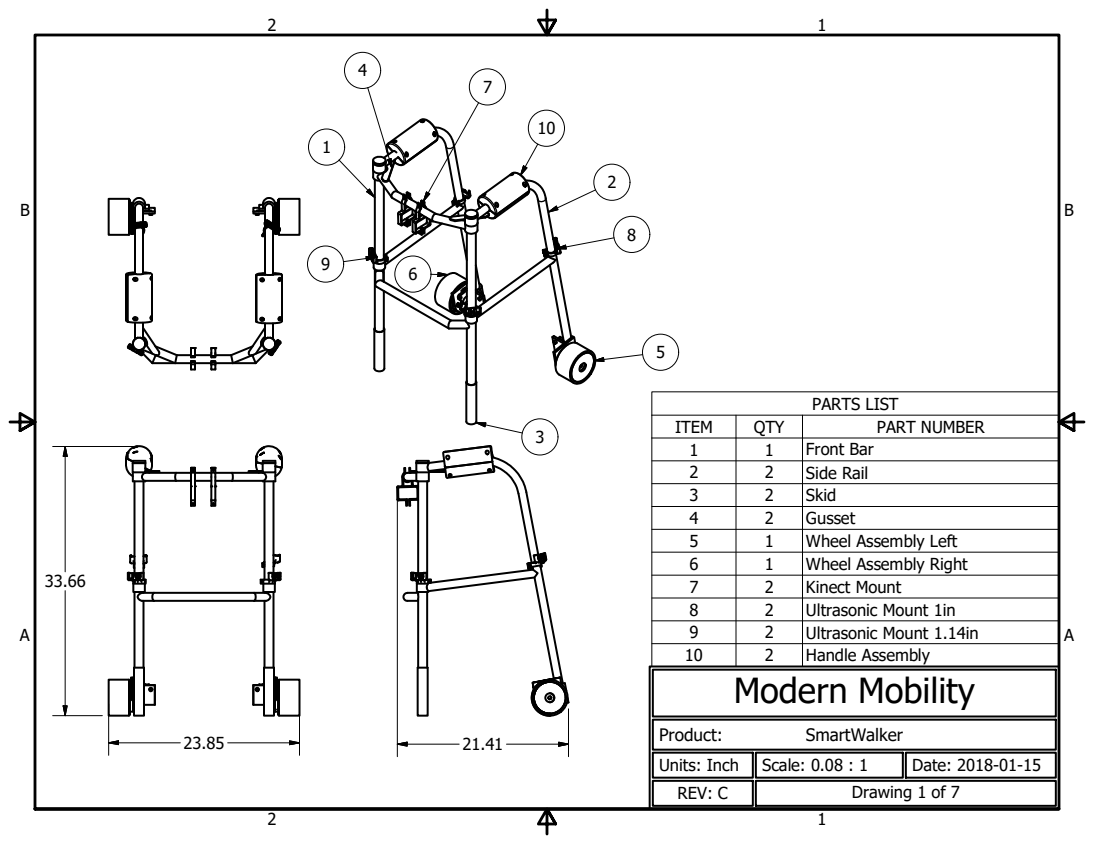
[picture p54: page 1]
PARTS LIST; Modern Mobility

ITEM | QTY | PART NUMBER
1 | 1 | Front Bar
2 | 2 | Side Rail
3 | 2 | Skid
4 | 2 | Gusset
5 | 1 | Wheel Assembly Left
6 | 1 | Wheel Assembly Right
7 | 2 | Kinect Mount
8 | 2 | Ultrasonic Mount 1in
9 | 2 | Ultrasonic Mount 1.14in
10 | 2 | Handle Assembly

Units: Inch | Scale: 0.08 : 1 | Date: 2018-01-15
REV: C | Drawing 1 of 7

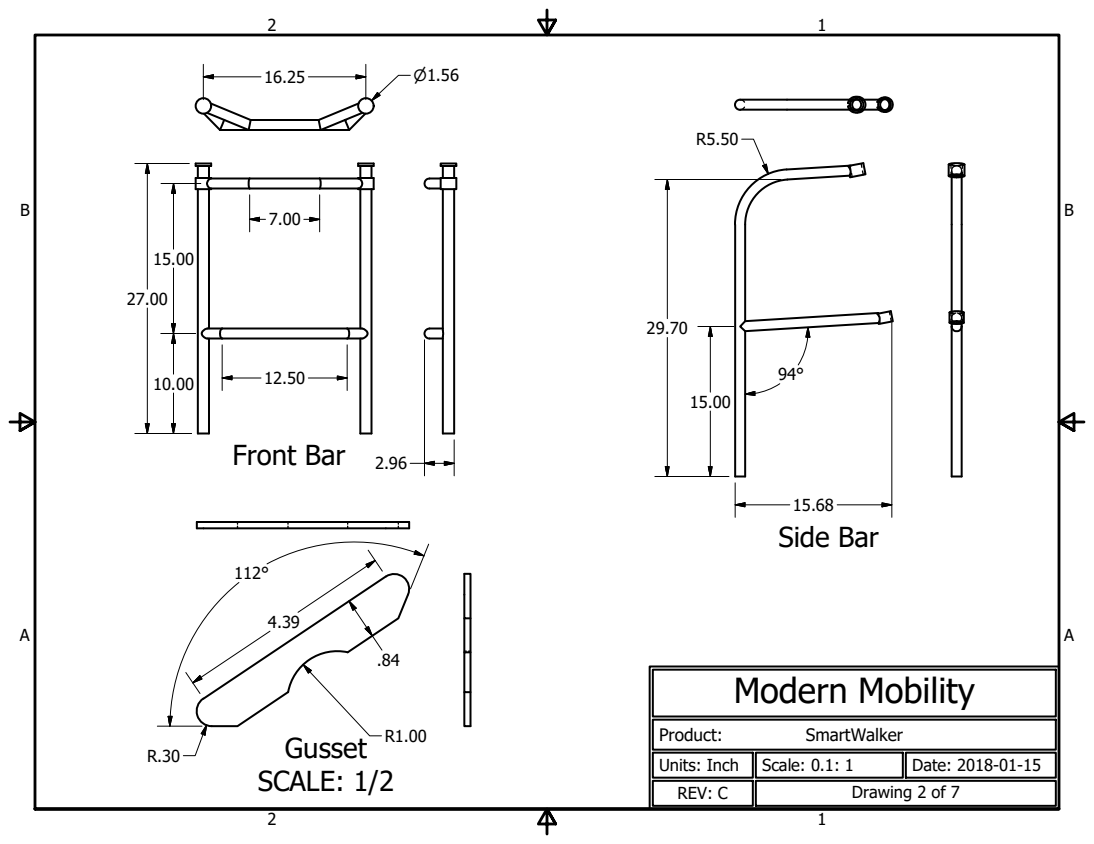
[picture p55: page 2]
Modern Mobility; Units: Inch; Scale: 0.1: 1; Date: 2018-01-15; Front Bar; Side Bar; SCALE: 1/2

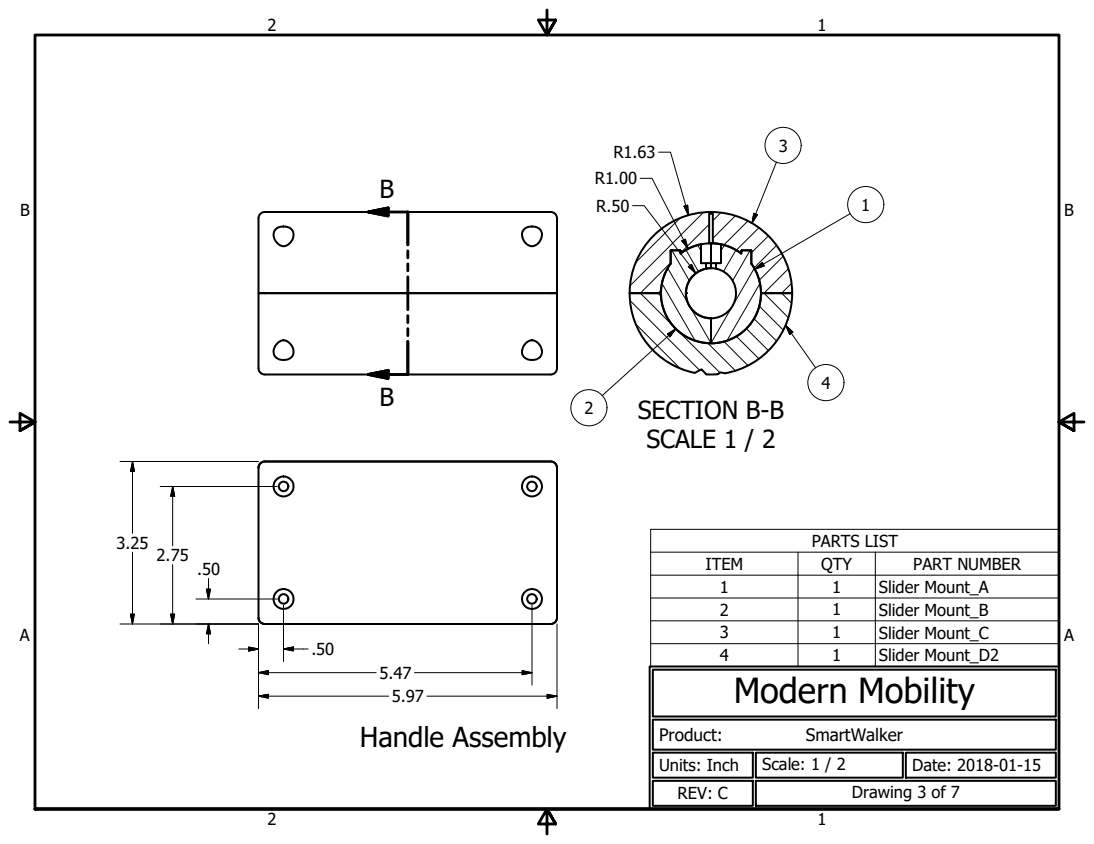
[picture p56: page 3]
SECTION B-B SCALE 1 / 2; PARTS LIST; Modern Mobility; Units: Inch; Scale: 1 / 2; Date: 2018-01-15; Handle Assembly

ITEM | QTY | PART NUMBER
1 | 1 | Slider Mount_A
2 | 1 | Slider Mount_B
3 | 1 | Slider Mount_C
4 | 1 | Slider Mount_D2

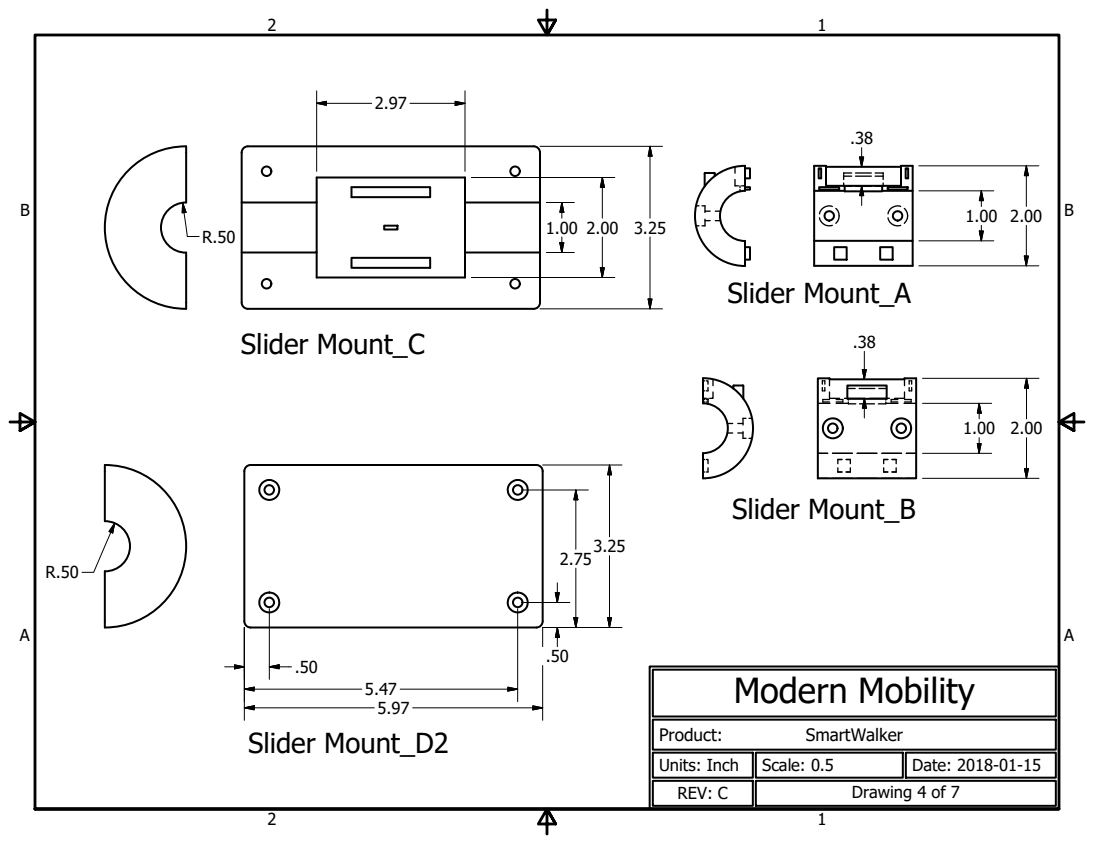
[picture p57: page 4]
Modern Mobility; Units: Inch; Scale: 0.5; Date: 2018-01-15; Slider Mount_A; Slider Mount_B; Slider Mount_C; Slider Mount_D2

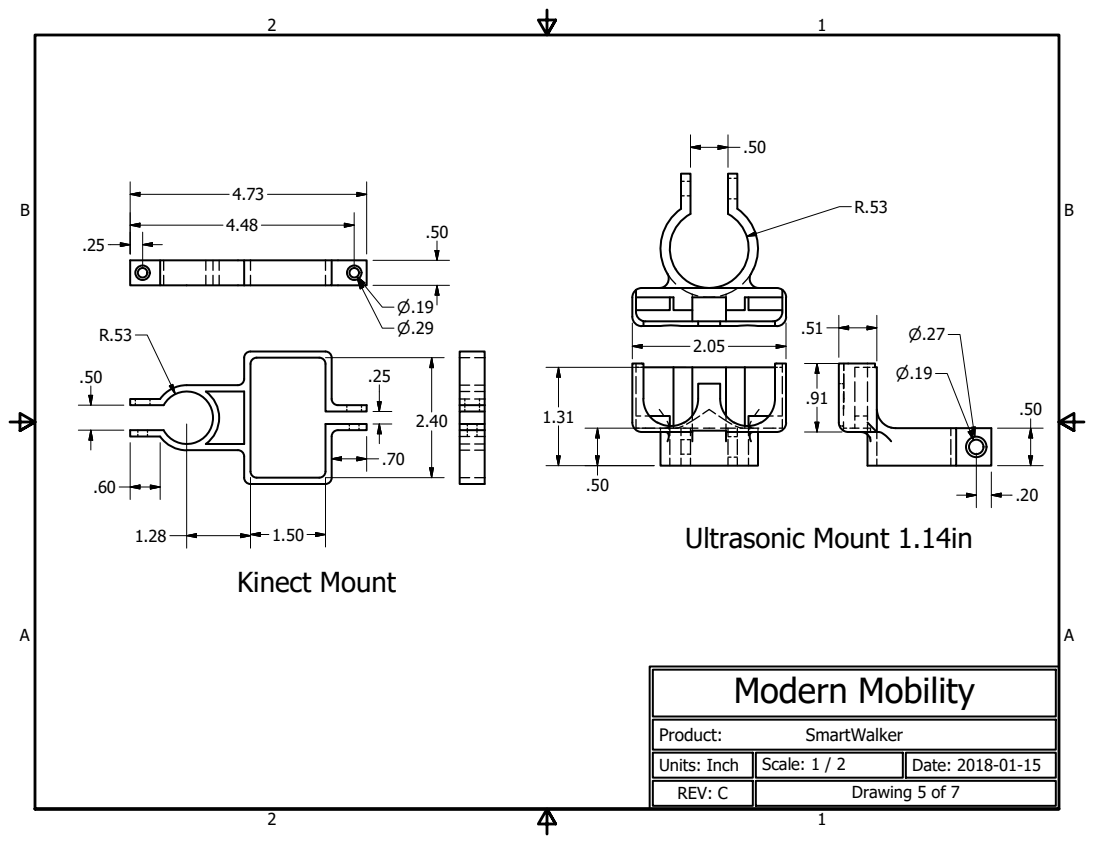
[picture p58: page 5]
Modern Mobility; Units: Inch; Scale: 1 / 2; Date: 2018-01-15; Kinect Mount; Ultrasonic Mount 1.14in

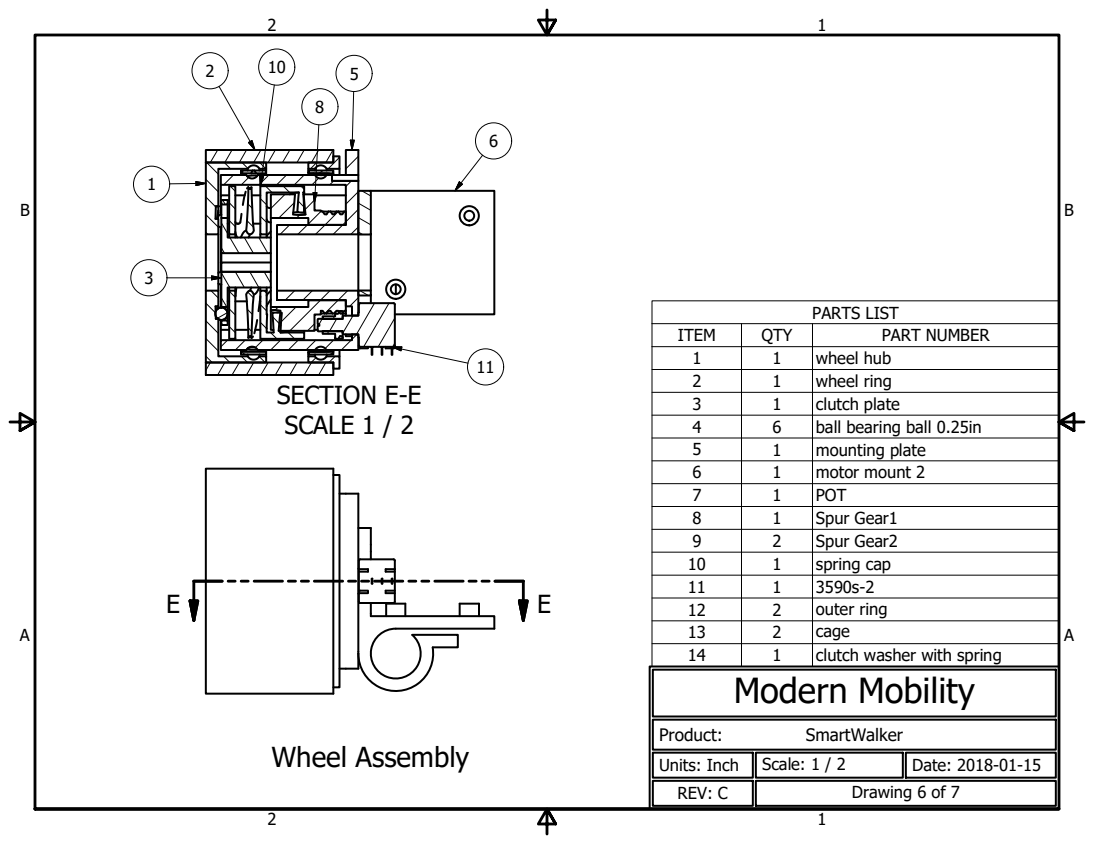
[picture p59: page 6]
SECTION E-E SCALE 1 / 2; PARTS LIST; ITEM; QTY; PART NUMBER; wheel hub; Modern Mobility; Units: Inch; Scale: 1 / 2; Date: 2018-01-15; Wheel Assembly

2 | 1 | wheel ring
3 | 1 | clutch plate
4 | 6 | ball bearing ball 0.25in
5 | 1 | mounting plate
6 | 1 | motor mount 2
7 | 1 | POT
8 | 1 | Spur Gear1
9 | 2 | Spur Gear2
10 | 1 | spring cap
11 | 1 | 3590s-2
12 | 2 | outer ring
13 | 2 | cage
14 | 1 | clutch washer with spring

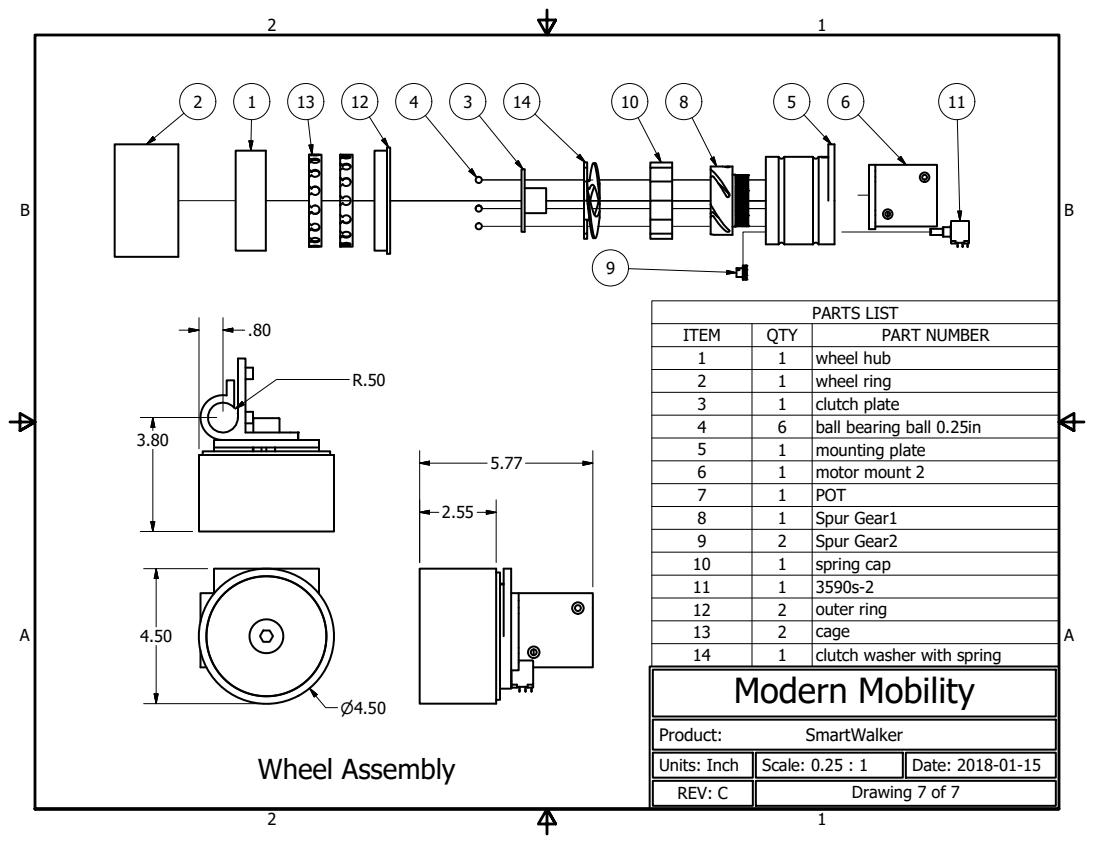
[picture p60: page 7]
PARTS LIST; Modern Mobility; Units: Inch; Scale: 0.25 : 1; Date: 2018-01-15; Wheel Assembly

ITEM | QTY | PART NUMBER
1 | 1 | wheel hub
2 | 1 | wheel ring
3 | 1 | clutch plate
4 | 6 | ball bearing ball 0.25in
5 | 1 | mounting plate
6 | 1 | motor mount 2
7 | 1 | POT
8 | 1 | Spur Gear1
9 | 2 | Spur Gear2
10 | 1 | spring cap
11 | 1 | 3590s-2
12 | 2 | outer ring
13 | 2 | cage
14 | 1 | clutch washer with spring

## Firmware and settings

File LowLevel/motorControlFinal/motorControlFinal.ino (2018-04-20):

/* LEFT MOTOR CONTROL MODULE */
//ModernMobility

/*
This software reads the value from each of the ultrasonic sensors and manual slider.
Every 10ms these values are sent back to the Raspberry Pi for processing 
*/

/*
Issues: The stop reset is not working. Could stem from the bytes potentially ariving after the 
first block of code with the Serial.available check. How can we make it so this cannot happen?
*/

#include <Arduino.h>
#include <PID_v1.h>    //Library details: https://playground.arduino.cc/Code/PIDLibrary
#include <Encoder.h>
//#include <Filters.h>
#define ENCODER_OPTIMIZE_INTERRUPTS

//Motor Pins
#define DIR1 6
#define PWM1 5

//Encoder Pins
#define ENC1 3
#define ENC2 4

//Encoder Parameters
#define SAMPLE_DELAY 10
#define PULSES_PER_TURN 512

/*  Constants */
//PID Constants
const double K_P = 330.15, 
             K_I = 20.05,
             K_D = 20,
             OUT_MIN = -255,  
             OUT_MAX = 255;
const int SAMPLE_TIME = 10;
bool pOnE = true;

//Serial Constants   
const byte START_FLAG = 0x7F,
           STOP_FLAG = 0x7E;
           
const float radius = 0.12065; //in meters

//Variables
double lastInput = 0;
unsigned long PID_lastTime = 0;
double outputSum = 0;
double Output, Kp_calc, error, dInput, Ki_calc;
double deadband = 0.075;

//PID values
float motorVelCmd = 0;
int MotorCmd = 0,
    initMotorCmd = 0, 
    initMotorDir = 0,
    lastMotorCmd = 0;

//Serial reading values
int byteRead = 0,
    sendEncoder = 0;
    
//Encoder reading values
unsigned int lastTime = 0, currentTime = 0; 
long lastPosition = 0;
float RPM = 0, wheelVel = 0;
int encoderVal = 0;
int encPosition  = 0;

unsigned int wheelVelOut;
int count = 0;
int period = 0;

Encoder myEncoder(ENC1, ENC2);

void setup() {
    Serial.begin(115200); // Starts the serial communication at 57600 baud (this is fast enough)
    //initPID();
    //Motor Outputs
    pinMode(DIR1, OUTPUT);  //Wheel motor direction
    pinMode(PWM1, OUTPUT);  //Wheel motor PWM

    digitalWrite(DIR1, HIGH); //direcitons  
    digitalWrite(PWM1, initMotorCmd);   //speed scale speed here with input from pi
}

void loop() {  
  // Receive new motor command or stop/start
  //sendFlag = 0;
  if (Serial.available()){
    //count = 0; 
    byteRead = Serial.read();
    switch (byteRead){
      case START_FLAG: sendEncoder = 1; break;
      case STOP_FLAG: sendEncoder = 0; break;
      default:  //Velocity command
        /*If byteRead is negative, its MSB will be 1 because 2s compliment. 
        * However, because arduino is dumb, it reads in bytes as 16-bit integers,
        * So, when you try to read the value, its 8 MSB are zero, making
        * Arduino think it is a positive number. We must set these bits to 1
        * (sign extension) to get it to recognize byteRead as negative.
        */
        if (byteRead & 0x0080) { //Is byteRead supposed to be negative?
            byteRead = byteRead | 0xFF00; //Sign extends byteRead to 16 bits
        }
        motorVelCmd = -float(byteRead)/100; //Converts cm/s value to m/s
        break;
    }
  }

    /*if (count > 1000){
      motorVelCmd = 0;
    }
    else {
      motorVelCmd = 0;
    }*/
  
  //UPDATE ENCODER
  encoderVal = myEncoder.read();
  encPosition = encoderVal;
  currentTime = (unsigned int)millis();
  if (currentTime - lastTime >= SAMPLE_DELAY) {
    RPM = ((lastPosition-encPosition) * (60000.f / (currentTime - lastTime))) / PULSES_PER_TURN/4;
    wheelVel = convertToLinearVel(RPM);
    lastTime = currentTime;
    lastPosition = encPosition;
    encPosition = 0;
  }

  //DO PID
  /* Graphing wheel velcoity */
  //Serial.print(encoderVal);Serial.println(" ");
  //Serial.println(motorVelCmd);

  unsigned long now = millis();
  if(now - PID_lastTime >= SAMPLE_TIME){
    /*Compute all the working error variables*/
    error = (double) motorVelCmd - wheelVel;
    dInput = (double) (wheelVel - lastInput);
    if (abs(error) <= deadband){
      Ki_calc = 0;
    }
    else{
      Ki_calc = K_I * error;
    }
    outputSum+= Ki_calc;
    if(outputSum > OUT_MAX) outputSum = OUT_MAX;
    else if(outputSum < OUT_MIN) outputSum = OUT_MIN;

    /*Add Proportional on Error, if P_ON_E is specified*/
    if(pOnE){
      if (abs(error) <= deadband){
        Kp_calc = 0;
      }
      else{
        Kp_calc = K_P * error;
      }
      Output = Kp_calc;
      }
    else Output = 0;

    /*Compute Rest of PID Output*/
    Output += outputSum - K_D * dInput;
    if(Output > OUT_MAX) Output = OUT_MAX;
    else if(Output < OUT_MIN) Output = OUT_MIN;
    MotorCmd = Output;
    /*Remember some variables for next time*/
    lastInput = wheelVel;
    PID_lastTime = now;
  }

  MotorCmd = 0;
  digitalWrite(DIR1, signPos(MotorCmd) ? HIGH : LOW);   //Assigning appropriate motor direction
  analogWrite(PWM1,abs(MotorCmd));                      //Actuate motor command
  //Send updated encoder value
  
  if (sendEncoder == 1) {
    Serial.write(byte(encoderVal & 0x00FF)); 
    Serial.write(byte((encoderVal >> 8) & 0x00FF));
  }
  delay(30);
}

/*******************************************************************************************************/

bool signPos(int value) {
  return (value >= 0); 
}

float convertToLinearVel(float rpm){
  return rpm*(2*M_PI/60.0)*radius;
}

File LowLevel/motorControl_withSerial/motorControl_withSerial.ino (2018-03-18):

/*
This software reads the value from each of the ultrasonic sensors and manual slider.
Every 10ms these values are sent back to the Raspberry Pi for processing 
*/


/*
Issues: The stop reset is not working. Could stem from the bytes potentially ariving after the 
first block of code with the Serial.available check. How can we make it so this cannot happen?
*/

#include <Arduino.h>
#include <PID_v1.h>    //Library details: https://playground.arduino.cc/Code/PIDLibrary
#include <Encoder.h>
#include <Filters.h>

#define ENCODER_OPTIMIZE_INTERRUPTS

//Motor Pins
#define DIR1 6
#define PWM1 5
//#define DIR2 7
//#define PWM2 8

//Encoder Pins
#define ENC1 9
#define ENC2 10

//Encoder Parameters
#define SAMPLE_DELAY (10)
#define PULSES_PER_TURN (512)

//Constants
const double K_P = 10, 
             K_I = 10,   //K values must be >= 0
             K_D = 0.1,
             OUT_MIN = -255,  
             OUT_MAX = 255,
             RAMP_DOWN_CMD = 100; 
const int SAMPLE_TIME = 20; 
const byte START_FLAG = 0x7F,
           STOP_FLAG = 0x7E;
const float radius = 0.1143; //in meters

//Variables
double PID_Input,              //The variable we are trying to control (from Motor Module)
       PID_Output,             //The variable that will be adjusted by the PID
       PID_SetPoint;    //The value we are trying to get to or maintain (from ROS node)
float motorVelCmd = 0;
int MotorCmd,
    lastMotorCmd = 0, 
    lastMotorDir = 0;
byte LSB,
     sendEncoder = 0;
int byteRead = 0;
unsigned int lastTime, currentTime; 
int lastPosition = 0;
float RPM, wheelVel;
long encoderVal;
long encPosition  = 0;

int encoderCount = 0;


float filterFrequency_encoder = 0.05;
FilterOnePole lowPassFilter_encoder(LOWPASS, filterFrequency_encoder);
PID MotorPID(&PID_Input, &PID_Output, &PID_SetPoint, K_P, K_I, K_D, DIRECT);
Encoder myEncoder(ENC1, ENC2);

void initPID(){
    MotorPID.SetMode(AUTOMATIC);                //Turns the PID on, default is off (MANUAL)
    MotorPID.SetOutputLimits(OUT_MIN, OUT_MAX); //By default this is (0, 255)
    MotorPID.SetSampleTime(SAMPLE_TIME);        //By default this is 200ms
    MotorPID.SetControllerDirection(DIRECT);
}
void setup() {
    Serial.begin(115200); // Starts the serial communication at 57600 baud (this is fast enough)

    initPID();

    //Motor Outputs
    pinMode(DIR1, OUTPUT);  //Wheel motor direction
    pinMode(PWM1, OUTPUT);  //Wheel motor PWM
    //pinMode(DIR2, OUTPUT);  //Brake motor direction
    //pinMode(PWM2, OUTPUT);  //Brake motor PWM
    //pinMode(0,INPUT);

    //digitalWrite(DIR1, lastMotorDir); //direcitons  
    //digitalWrite(DIR2, 0);
    //digitalWrite(PWM1, lastMotorCmd);   //speed scale speed here with input from pi
    //digitalWrite(PWM2, 0);
}

void loop() {  
    // Receive new motor command or stop/start
    //sendFlag = 0;
    /*if (Serial.available()) {
      byteRead = Serial.read();
      switch (byteRead){
        case START_FLAG: sendEncoder = 1; break;
        case STOP_FLAG: sendEncoder = 0; break;
        default:  //Velocity command
          /*If byteRead is negative, its MSB will be 1 because 2s compliment. 
          * However, because arduino is dumb, it reads in bytes as 16-bit integers,
          * So, when you try to read the value, its 8 MSB are zero, making
          * Arduino think it is a positive number. We must set these bits to 1
          * (sign extension) to get it to recognize byteRead as negative.
          */
          /*if (byteRead & 0x0080) { //Is byteRead supposed to be negative?
              byteRead = byteRead | 0xFF00; //Sign extends byteRead to 16 bits
          }
          motorVelCmd = float(byteRead)/100; //Converts cm/s value to m/s
          break;
      }  
    }*/
    //motorVelCmd = 0;
    MotorCmd = 100;
    //UPDATE ENCODER
    encoderVal = myEncoder.read();
    //Serial.print("Encoder = ");Serial.print(encoderVal);
    //lowPassFilter_encoder.input(encoderVal);
    //encPosition = lowPassFilter_encoder.output();

    //if (encoderCount >= 5){
    currentTime = (unsigned int)millis();
      //if (currentTime - lastTime >= SAMPLE_DELAY) {
        Serial.print("lastPosition = ");Serial.print(lastPosition);Serial.print(" encoderVal = ");Serial.print(encoderVal);
        Serial.print("  currentTime = ");Serial.print(currentTime);Serial.print("  lastTime = ");Serial.println(lastTime);
        RPM = (60000.f * (lastPosition-encoderVal)) / ((currentTime-lastTime)*PULSES_PER_TURN);
        wheelVel = convertToLinearVel(RPM);
        lastTime = currentTime;
        lastPosition = encoderVal;
        encoderVal = 0;
        //Serial.print(" RPM = ");Serial.println(RPM);
      //}
   //}
    
    //DO PID
    PID_Input = wheelVel;
    PID_SetPoint = (double) motorVelCmd;
    //MotorCmd = doPID(lastMotorCmd);

    lastMotorCmd = MotorCmd;                              //Set previous motor command to current motor command
    
    digitalWrite(DIR1, signPos(MotorCmd) ? HIGH : LOW);   //Assigning appropriate motor direction
    analogWrite(PWM1,abs(MotorCmd));                      //Actuate motor command

    /*
    Serial.println(encPosition);
    Serial.print(" "); //For plotting purposes*/
     
    //Send updated encoder value
    if (sendEncoder == 1) {
      Serial.write(byte(encoderVal & 0x00FF)); 
      Serial.write(byte((encoderVal >> 8) & 0x00FF));
      //Serial.write(0x0000);
    }
    delay(1);
}

int doPID(int previousMotorCmd){
    int newMotorCmd;
    /*
     * MotorPID.Compute() computes the PID and returns true, 
     * if it does not compute anything it will return false
     */
     if (!MotorPID.Compute()) {
      MotorCmd = 0.0;  //Send invalid value when nothing computed
     }
     else {
      newMotorCmd = (int)PID_Output;
      //Serial.println(Output);
      //Serial.print(" "); //For plotting purposes*/
      if (newMotorCmd >= 255){
        newMotorCmd = 255;
      }else if (newMotorCmd < -255){
        newMotorCmd = -255;
      }
     }
     return MotorCmd = newMotorCmd;
     //return MotorPID.Compute() ? (previousMotorCmd - (int)Output) : NULL;
     //MotorPID.Compute();
     //MotorCmd = Output;
}

bool signPos(int value) {
  return (value >= 0); 
}

float convertToLinearVel(float rpm){
  return rpm*(2*M_PI/60.0)*radius;
}

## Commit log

2017-11-19 Added requirements documents and such
    [DOC0001-.xlsx]
2017-11-19 deleted duplicated files
    [DOC0001-.xlsx]
2017-11-19 Kinect distance testing data
    [KinectTestMeasurements.xlsx]
2017-11-19 updated master list
    [DOC0001-.xlsx]
2017-11-30 added Wheel assembly CADs
    [3590s-2.ipt, 3590s-2.stp, Assembly2.0020.iam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]
2017-12-03 Changed and organized doc folders, and modified readME for ROS with more instructions
    [DOC0001-.xlsx, KinectTestMeasurements.xlsx]
2017-12-03 Commiting modified ROS readME
    [DOC0001-.xlsx, KinectTestMeasurements.xlsx]
2017-12-13 App can enable/disable device BT, discover BT devices, make itself discoverable, pair and start service connection.
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2018-01-05 Created a package for the ultrasound and motor control nodes 'node_test_1', complete with CMAKE and launch files
2018-01-05 Added the differential drive package to the launch file and added the catkin compatible version of the differential drive package to the repo. Parameters of the differential drive package were modifi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
2018-01-05 Correct upload of differential drive package
    [diff_tf.py]
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2018-01-06 made a mistake with the intsall header, fixed it and made instructions more clear
    [i2cpp.cpp]
2018-01-07 Wheel assembly verison 3
    [3590s-2.stp, ANSI (in).dwg, ANSI (in).idw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]
2018-01-07 Wheel assembly managed to delete a part
    [Wheel Assembly.0034.iam, Wheel Assembly.iam, wheel hub.0006.ipt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]
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2018-01-08 Added washer in cad
    [mounting plate.stl, washer.ipt, washer.stl]
2018-01-08 Fixed conversion of integers to bytes for communication
    [Arduino_Ultrasound.ino]
2018-01-09 Added slider code to the ultrasonic arduino code. Again, pin values need to be modified after wiring
2018-01-10 mounting plate edit
    [mounting plate.0022.ipt, mounting plate.ipt, mounting plate.stl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]
2018-01-10 i think i changed something
    [mounting plate.stl, washer.stl, wheel hub.stl]
2018-01-10 Started MotorPID.ino file
    [KinectTestMeasurements.xlsx, MiscCalcs.xlsx]
2018-01-10 sensor mounts
    [Ultrasonic Mount.ipt]
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2018-01-10 Fixed PID code and updated slider code
    [MotorPID.ino, Slider_and_Ultrasonic_Arduino.ino]
2018-01-11 edit sensor mount
    [Ultrasonic Mount.0002.ipt, Ultrasonic Mount.ipt, Ultrasonic Mount.stl]
2018-01-11 Removed PID from Raspberry Pi. Modified Ultrasonic node to account for reading and publishing slider information. Modified motor controller node to receive and send slider information as well as send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
2018-01-12 Fixed velocity selection nodes. Made left and right velocity selection nodes. Configured connection with rest of ROS network
    [l_wheelController.cpp, leftVelocitySelection.cpp, r_wheelController.cpp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]
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2018-01-13 Added references, comments and created seperate thread when establishing a Bluetooth connection to avoid frame skipping in the main activity
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2018-01-13 changed sensor mounts
    [Ultrasonic Mount 1.14in.0002.ipt, Ultrasonic Mount 1.14in.ipt, Ultrasonic Mount 1.14in.stl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]
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2018-01-14 added Handle slider CADs
    [Slider Mount.0002.ipt, Slider Mount_A.0009.ipt, Slider Mount_A.ipt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]
2018-01-14 walker CAD
    [3590s-2.0001.ipt, 3590s-2.ipt, POT.0001.ipt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]
2018-01-14 color change
    [motor mount 2.0009.ipt, motor mount 2.0010.ipt, motor mount 2.ipt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]
2018-01-14 update handle STLs
    [Slider Mount_A.stl, Slider Mount_B.stl, Slider Mount_C.stl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]
2018-01-14 created technical drawings
    [Hamdle Assembly.0001.iam, Handle Assembly.iam, Slider Mount_A.0009.ipt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]
2018-01-14 resolved dependency issues
    [Walker Assembly.0010.idw, Walker Assembly.0012.idw, Walker Assembly.0013.iam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]
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2018-01-15 draft drawings changes
    [Walker Assembly.0012.idw, Walker Assembly.0014.iam, Walker Assembly.0014.idw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]
2018-01-16 Added document explaining how to encapsulate and unencapsulate serial data
    [PPP-SerialWrappingExplained.xlsx]
2018-01-17 edits to draft drawings
    [Walker Assembly.newVer.idw]
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2018-01-18 Reviewed Nathan's last two commit in order to resolve merge conflicts for the MotorPID.ino file
    [MotorPID.ino]
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2018-01-21 tweaks to wheels
    [Spur Gear21.stl, Walker Assembly.0014.idw, Walker Assembly.0015.idw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]
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2018-01-24 Handle CADS updated
    [PPP-SerialWrappingExplained.xlsx, Slider Mount_A.ipt, Slider Mount_A.stl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]
2018-01-25 fixed ROS library inconsistencies
    [PPP-SerialWrappingExplained.xlsx]
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2018-01-25 changes to compact clutch wheel
    [Part1.ipt, Part1.stl, Part2.ipt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]
2018-01-25 making a new wheel
    [motor mount 2.ipt]
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2018-01-26 alternate wheel
    [Assembly1.iam, microServo-sg90.ipt, microServo-sg90.stl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]
2018-01-28 outer ring with cap
    [outer ring end stop.ipt]
2018-01-28 Edited the move_base configuration files to match our localization strategy. Changed the joystick publish name to cmd_vel to match move_base, and made twist_to_motors subscribe to cmd_vel. The graph 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
2018-02-03 Handle CADS .iges and .step exports
    [Slider Mount_A.iges, Slider Mount_A.step, Slider Mount_B.iges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]
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2018-02-15 updated kinect verification data for use in V&V doc
    [KinectTestMeasurements.xlsx]
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2018-03-01 Docs and stuff
    [KinectTestMeasurements.xlsx, UltrasonicAndEncoderTest.xlsx]
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2018-03-02 motor mount CADS
    [left_motor_mount.ipt, left_motor_mount.stl, right_motor_mount.ipt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]
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2018-03-18 Added several print statements to help localize error causes during debugging
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2018-03-20 added animation for new assembly cad
    [0_375_Hex_ID_x_1_125_OD_x_0_313_WD_Flanged_Bearing_217-2735.0001.ipt, 0_375_Hex_ID_x_1_125_OD_x_0_313_WD_Flanged_Bearing_217-2735.STEP, 0_375_Hex_ID_x_1_125_OD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]
2018-03-20 changes to assembly
    [Assembly2.0001.ipn, Assembly2.ipn]
2018-03-26 modified excel file
    [MiscCalcs.xlsx]
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2018-03-27 caster wheel mount
    [Mount.ipt]
2018-03-27 caster wheel mount update
    [Mount.0001.ipt, Mount.ipt]
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2018-03-28 caster wheel shims
    [Mount.stl, shim 10 Deg.0002.ipt, shim 10 Deg.ipt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]
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2018-04-05 added wheel lock
    [aluminum lock.ipt, aluminum lock.stl, shim 10 Deg.0002.ipt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]
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2018-04-09 recalculated ticks per meter because of new wheel tread
    [MiscCalcs.xlsx]
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2018-04-11 new aluminum lock
    [aluminum lock.0001.ipt, aluminum lock.ipt, aluminum lock.stl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]
2018-04-18 changes to encoder mount
    [Encoder mount_left.ipt, Encoder mount_left.stl, Encoder mount_right.ipt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]
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2018-04-20 updated Arduino code to reset Encoder values after ~30s
    [leftMotorControl.ino, rightMotorControl_V2.ino]
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2018-04-25 ticks per meter calculations
    [MiscCalcs.xlsx]
2018-04-26 fixed yaw calculation
2018-04-26 fixed calculations using rvec, in short solution was to convert rvec into rodrigues matrix using opencv function, then use that to construct 3x4 projection matrix, then use opencv function decomposeP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
2018-04-27 reversed yaw rotation direction and got map to close when a key is pressed
